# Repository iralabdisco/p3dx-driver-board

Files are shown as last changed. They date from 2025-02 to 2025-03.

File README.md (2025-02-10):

# p3dx-driver-board
An effort to reverse-engineer the Adept MobileRobots Pioneer-3DX's driver board.

## Rationale

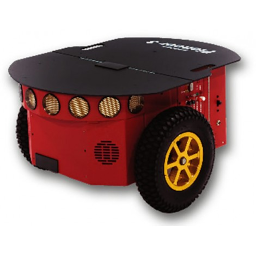
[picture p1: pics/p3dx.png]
p3dx


The [P3DX](https://www.generationrobots.com/media/Pioneer3DX-P3DX-RevA.pdf) is a nice, featureful, and self-contained robotics platform that was released sometime in the early '00s. We have three of those in our laboratory, and they're currently big red paperweights, as their SDK is no longer mantained; to my knowledge, the ROSARIA module that was used with ROS1 to control those robots has not been ported to ROS2, and their ARIA protocol is not documented.

There've been some efforts to produce libraries that can interface with the on-board microcontroller by figuring out how the protocol works, like [Purdue's P2OS driver](https://github.com/allenh1/p2os/tree/main), which is an open-source module for ROS that includes an ARIA driver -- their (C++) packet driver is under `p2os_driver/packet` and `p2os_driver/sip`.

I like the construction and the modularity of the P3DX: the driver board is completely separated from the MCU board, probably because the original designers already had upgradability in mind, and they're connected through a ribbon cable. Since the MCU board is not integral to the operation of the robot's electronics, I decided to figure out the pinout of the ribbon cable so that we could try to attach a different MCU or a Raspberry Pi to the driver board without too much effort, so that our students may still play with the P3DXes and learn from their operation.

## Architecture

The driver board has:
- Power control and generation circuitry for the +12V and +5V rails;
- Two H-bridges -- one for each motor;
- Connections for IR sensors and encoders;
- Optional connections for a fan, a charger, and temperature sensors to be mounted on the motors;

There are a couple of ICs on the board: two STM TD340 MOSFET drivers to control the H-Bridge, a couple of STM TS922I Op-Amps, and two TI SN74HC14 Schmitt-Trigger Inverters. Look under the [datasheets/](datasheets/) folder if you need to look something up.

## Disclaimers

Obligatory disclaimers:
- I take absolutely no credit for the design of the driver board.
- This was an independent effort I made in my spare time; my institution is not affliated with this in any way, shape, or form.
- I decided to release the schematics I came up with under Public Domain because, as far as I know, this platform has been long since abandoned. If you feel like this is infringing your IP rights, please file a DMCA request and I'll take this down.

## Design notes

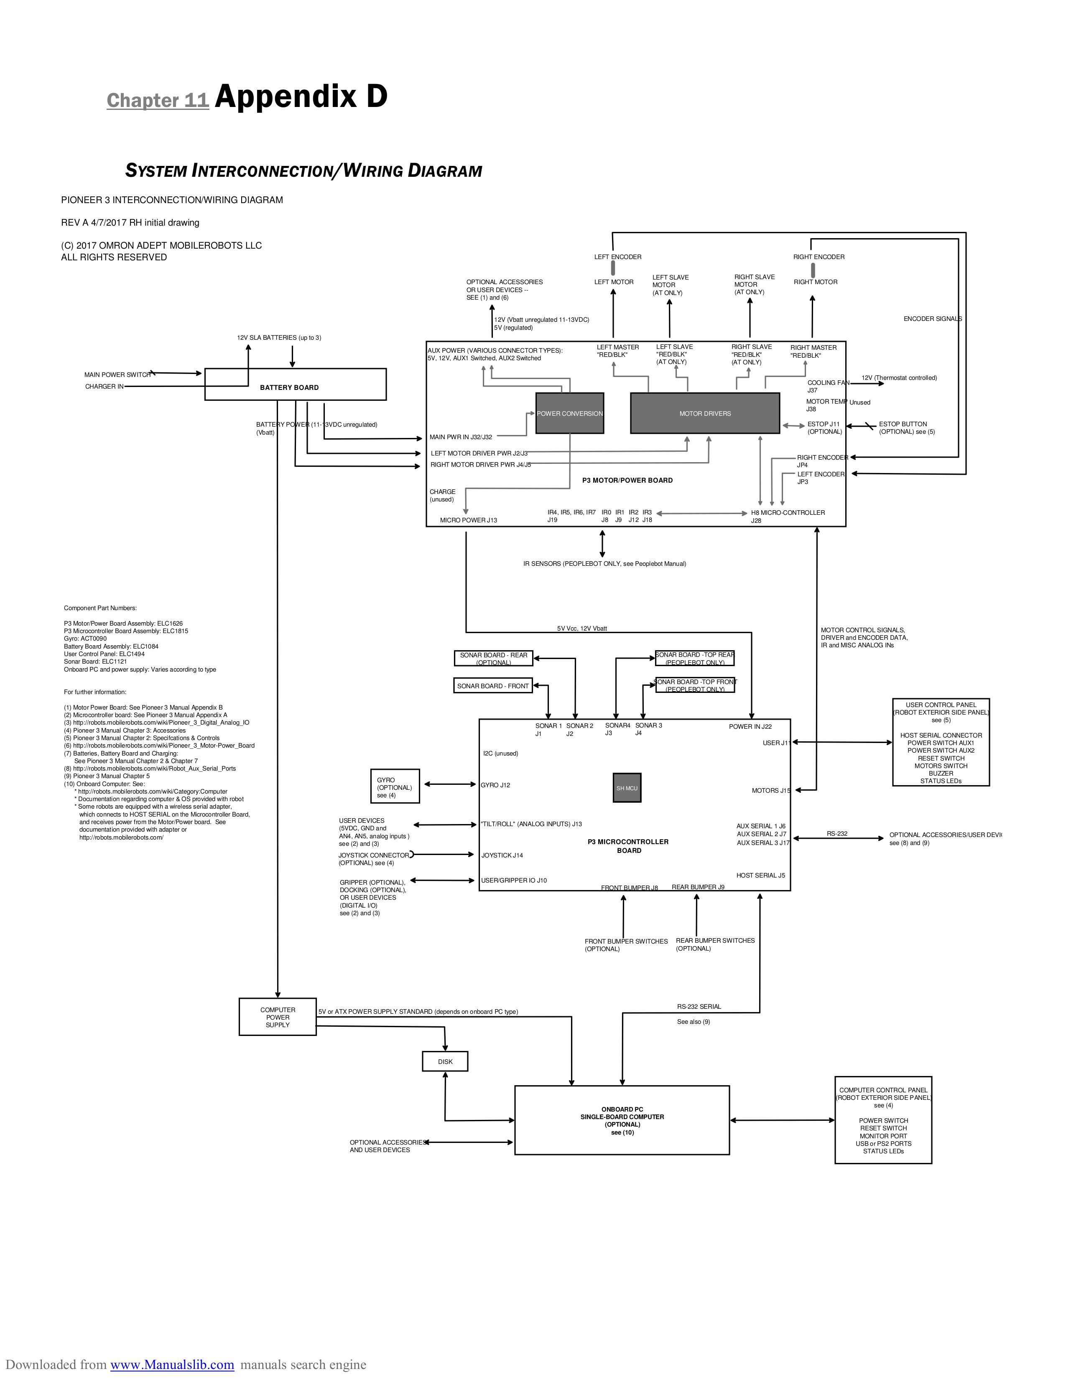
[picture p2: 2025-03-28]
datasheets/system_interconnection.jpg

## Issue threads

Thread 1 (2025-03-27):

Funzionamento Ponte-H (TD340)

giuseppe-caliaro, 2025-03-27:
Il circuito integrato ST TD340 permette il pilotaggio di un motore DC attraverso un ponte-H.
Di seguito il diagramma a blocchi e la descrizione del pinout.

_**Diagramma a blocchi/Descrizione pinout TD390**_

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

Punti chiave appresi:
L1/L2 = Pilotano i gate dei mosfet low-side del ponte-H, Q1L e Q2L rispettivamente in figura.
H1/H2 = Pilotano i gate dei mosfet high-side del ponte-H, Q1H e Q2H rispettivamente in figura.
S1/S2 = Costituiscono insieme a CB1 e CB2 il circuito di bootstrap, necessario quando il

Closed 2025-03-28.

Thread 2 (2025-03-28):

Funzionamento TD340 (Motor Driver)

giuseppe-caliaro, 2025-03-28:
Il circuito integrato ST TD340 permette il pilotaggio di un motore DC attraverso un ponte-H.
Di seguito il diagramma a blocchi e la descrizione del pinout.

**_Diagramma a blocchi/Descrizione pinout TD340_**
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

**Punti chiave appresi:**

- L1/L2: Pilotano i gate dei mosfet low-side del ponte-H, Q1L e Q2L rispettivamente in figura.

- H1/H2: Pilotano i gate dei mosfet high-side del ponte-H, Q1H e Q2H rispettivamente in figura.

- S1/S2: Costituiscono insieme a CB1 e CB2 il circuito di bootstrap del ponte H.
Il circuito di boostrap è necessario per superare la tensione di soglia (Vgate - Vsource) del mosfet high-side quando quest'ultimo è ON.
Perchè è necessario? È necessario perchè in questa configurazione Source del mosfet high-side è a 12V, quindi non si raggiungerebbe la tensione di soglia minima per garantire l'attivazione mosfet.
Diversamente nei mosfet low-side ciò non accade, essendo source a GND quando i mosfet low-side sono attivi.
vedi https://www.homemade-circuits.com/h-bridge-bootstrapping

- IN1/IN2: Questi pin sono utilizzati per controllare velocità (IN1) e direzione (IN2) del motore. La modalità "freno" è attivata quando ci sono 0V sul pin IN1 per piu di 200 microsecondi.

**Questioni aperte:**

1. Nel circuito sono presenti due Op-Amp U6A/U6B (fisicamente uno solo, Op-Amp TS9221 presenta due ingressi invertenti, due ingressi non invertenti e due output). Non mi è completamente chiaro il loro utilizzo.
U6A sembra essere configurato come comparatore (vedi partitore di tensione su ingresso invertente)
U6B avendo una retroazione positiva (vedi Vout applicata a ingresso non invertente) sembra essere un comparatore con isteresi (Trigger di Schmitt).
L'uscita dell'Op-Amp U6B controlla la base di un BJT, il quale agisce come interruttore per i segnali RIGHT_C1 e RIGHT_C2 provenienti dalla MCU.

Non mi è chiaro il motivo del collegamento del Drain di Q5 con il circuito sopra citato.
Non trovo riscontro di continuità con questo collegamento _DrainQ5 - R36 - Ingresso non invertente U6A_ ,  mentre trovo riscontro di continuità con _SourceQ7 - R36 - GND_ , il mosfet Q7 costituisce parte del low-side del ponte H quindi è sensato che il Source sia a GND.

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

Per un controllo di base del TD340, IN1 e IN2 sono sufficienti, tuttavia, la comprensione del circuito sopra descritto penso sia fondamentale per decifrare la logica di controllo dei segnali MCU verso il TD340.

jack23247, 2025-03-28:
Ottimo lavoro.

Ti lascio qui una risorsa interessante sui ponti H: https://www.modularcircuits.com/blog/articles/h-bridge-secrets/

Per quanto riguarda Q5, ci guardiamo insieme quando posso. Gli opamp anche, ma non sono molto ferrato.. quattro occhi sono sempre meglio di due però

giuseppe-caliaro, 2025-03-28:
Credo di aver capito che:
Gli ingressi degli operazionali sono collegati a Source di Q7 e Q8 (low-side), attraverso questi mosfet scorre la corrente che scorre attraverso il motore.
Interposta tra questo collegamento è posizionata una resistenza di shunt (R2 nello schema), la quale viene normalmente utilizzata come misuratore di corrente (qui una discussione circa la misurazione di corrente attraverso l'utilizzo di una resistenza di shunt https://electronics.stackexchange.com/questions/152500/measure-current-through-h-bridge-using-shunt).

La caduta di tensione ai capi della resistenza di shunt è proporzionale alla corrente che scorre attraverso i mosfet.
Se si dovesse verificare un overcurrent, causerebbe una caduta di tensione, probabilmente sotto una certa soglia dimensionata nell'implementazione degli op-amp. Questa caduta di tensione pilota il BJT, bloccandone la conduzione e interrompendo cosi i segnali RIGHT_C1 e RIGHT_C2.

Sostanzialmente mi sembra di aver capito che è un circuito di protezione da overcurrent.

giuseppe-caliaro, 2025-03-28:
Condivido il nuovo schema (Right motor driver) aggiornato con le correzioni riguardanti gli op-amp discussi precedentemente:

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

giuseppe-caliaro, 2025-03-29:
**Ulteriori note interessanti circa il funzionamento del driver TD340:**

- Frequenza di switching: 25kHz

- Lavora con una tensione tra 6.5V e 18.5V

- Da datasheet: _"The speed control (or duty cycle) is achieved by the Low Side Drivers which impose the PWM function while the cross-corresponding High Side MOSFETS is kept fully ON."_.
Questa tecnica consiste nell'applicare il segnale PWM ai mosfet low-side, cioè quelli connessi a massa, mentre i mosfet high-side, cioè quelli connessi alla tensione di alimentazione, vengono mantenuti sempre ON.

- Ci sono 4 pin che forniscono servizi aggiuntivi:

1. **Reset**: TD340 fornisce un circuito di supervisore di tensione, il quale riavvia il microcontrollore quando la tensione di quest'ultimo scende sotto una soglia di 4.2V, e l'uscita Reset resta a LOW fino a quando la tensione non supera i 4.3V, dopodichè il microcontrollore riprende la sua normale esecuzione.

1. **Watchdog** (WD nello schema): TD340 fornisce un circuito di watchdog, il quale resetta il driver per evitare che il sistema rimanga bloccato in caso di errori software/hardware. Watchdog controlla che il microcontrollore invii segnali costanti al pin WD, se questi impulsi non avvengono per un periodo troppo lungo (timeout, settabile attraverso il dimensionamento di un condensatore), questo blocca il sistema finchè il microcontrollore non riprende ad inviare impulsi al pin WD.

1. **Temp**: TD340 fornisce un indicatore di temperatura.

1. **Standby** (STBY nello schema): TD340 può essere messo in standby mode tramite software, i mosfet vengono spenti. Questo permette di ridurre il consumo a 200 microAmpere. Per uscire da questa modalità il sistema ha bisogno di 20 ms per caricare il condensatore facente parte del circuito di boostrap. Il driver non deve ricevere segnali IN1 e IN2 prima che il condensatore sia completamente carico, altrimenti i mosfet high-side potrebbero non funzionare correttamente.

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

Da schema i sopracitati pin ad eccezione di Standby risultano però essere stati esclusi nel design della driver-board.
La configurazione di Standby come accennato non risulta essere esclusa, tuttavia dal connettore del microcontrollore non sembra essere presente un pin designato a questa funzione:

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

Questa questione è cruciale per la sicurezza e l'affidabilità complessiva del sistema, poiché, con l'esclusione dei pin relativi a Reset e Watchdog nel design della driver-board, la gestione delle sicurezza e affidabilità è completamente delegata al microcontrollore STM32F767ZI (MCU scelta per pilotare la driver-board).
Credo quindi che sarà necessario tenere conto di questo aspetto in fase di sviluppo.

jack23247, 2025-03-31:
Ottimo lavoro. Alcune osservazioni:

- Bello e leggibile lo schema. Al posto del motore però metterei il connettore, dato che il motore non è tecnicamente parte della scheda. Possiamo comunque mettere il motore in un box per chiarezza.
- Avevo notato anche io il fatto che non è stato usato il circuito di Watchdog interno ai TD340. Non so il perché di questa scelta, ma sicuramente ci sarà stato un motivo ingegneristicamente valido. Comunque teniamone conto.

Per quanto riguarda i "salti", quando passo in lab ci guardiamo insieme!

giuseppe-caliaro, 2025-03-31:
Perfetto, allora modifico lo schema sostituitendo il motore con il connettore.

Per la questione watchdog magari studiando l'interfacciamento tra la nostra board e la driver-board salta fuori il motivo dell'esclusione di questi pin.

giuseppe-caliaro, 2025-03-31:
Il modello è: **Renesas SH2-7144 RISC 32-bit**.
Documentazione: https://www.renesas.com/en/document/mah/sh7144-group-sh7145-group-hardware-manual?r=1054851

Che succede se imposti il duty cycle del PWM a zero? E come passi, in generale, il segnale PWM al driver?

Impostando il duty cycle del PWM a zero mi aspetto che il Driver setti a 0V il motore.

In generale, penso che il microprocessore della Nucleo generi il segnale PWM (attraverso un timer).
La Nucleo sarà collegata, attraverso il connettore specifico, alla driver-board, la quale invia il segnale PWM al pin del Driver.

jack23247, 2025-03-31:
Ottimo! Allora possiamo gestirlo così anche noi, secondo me.

giuseppe-caliaro, 2025-04-01:
> * STBY è attivo basso (ha la linea sopra), quindi se non erro R41 fa da resistenza di pull-up e fondamentalmente esclude la funzionalità di Stand-by.

Grazie per la precisazione

Closed 2025-05-22.

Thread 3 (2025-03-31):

Motor Encoder

giuseppe-caliaro, 2025-03-31:
Prima di analizzare il connettore J28, cioè il connettore che collega MCU-board e driver-board e permette di scambiare segnali tra di essi, è secondo me necessario approfondire prima i segnali che il sopracitato connettore trasporta e come quest'ultimi sono generati.
Nella issue relativa all'integrato TD340 ho analizzato i segnali che arrivano da J28 al driver che infine pilota i motori, cioè IN1 e IN2.

In questa issue analizzerò i connettori JP3 e JP4, che al contrario dell'integrato TD340, inviano segnali dai motori al microprocessore, cioè i segnali di encoding.

Di seguito lo schema dei pin del connettore J28:

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
Questa issue descrive i pin: 6, 8, 10, 12, cioè rispettivamente:

- Left encoder channel A

- Right encoder channel A

- Right encoder channel B

- Left encoder channel B

La driver-board del Pioneer P3DX offre un encoder ottico a quadratura, detto anche incrementale, il quale genera sulle sue uscite due segnali A e B, cioè due onde quadre con un duty cycle del 50% sfasate di 90°

Per conoscere se il motore gira in senso orario o antiorario, si confrontano le due fasi di A e B.
Sul fronte di discesa della fase A, se il valore logico di B è 1, il motore sta ruotando in senso orario, viceversa, cioè se il fronte di discesa di A corrisponde al valore logico di B 0, il motore sta ruotando in senso antiorario:

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
**_Senso orario/Senso antiorario_**

---

Da manuale operativo (Pag. 67) , ho trovato i seguenti dati che secondo me saranno utili in fase di sviluppo firmware per ottenere valori di velocità/rotazione/distanza percorsa ecc. :

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
- **Encoders**: 500-count quadrature optical encoder on each motor: l'encoder quindi genera 500 impulsi (A e B) per ogni giro completo del motore
- **Quadrature encoder count/wheel revolution**: 19,150 (200mm wheel): l'encoder genera 19.150 impulsi per ogni giro completo di ruota assumendo che quest'ultima abbia un diametro di 200mm.
- **Quadrature encoder counts/mm robot linear distance travelled**: 128: l'encoder genera 128 impulsi per millimetro di distanza percorsa.
- **Quadrature encoder counts/360° robot rotation**: 33,140: l'encoder genera 33.140 impulsi per una completa rotazione di 360° sul suo asse.

---

Di seguito riporto lo schema degli encoder presenti sulla driver-board:

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

I segnali, rispettivamente dal pin 1 e 8 dell'encoder, passano attraverso un'integrato, il 74HC14, cioè un Trigger di Schmitt.
Il Trigger di Schmitt produce in uscita un'onda quadra "pulita" da rumore ed eventuali oscillazioni e squadra perfettamente il segnale fornito dagli encoder.

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

Successivamente il segnale è fornito al microprocessore attraverso i segnali EL1, EL2, ER1, ER2, pronti per essere processati.

giuseppe-caliaro, 2025-03-31:
Mastering STM32 2.0.1 Pag. 325 paragrafo 11.3.9 **Encoder Mode**  spiega come gestire segnali di encoder in quadratura.
Segnali di encoder in quadratura possono essere gestiti con degli interrupt "_using interrupts
to capture when the channel changes status_", oppure usando dei timer.

STM32 fornisce fornisce anche una modalità dei timer detta  _encoder mode_.
Questa modalità offre, settando in modo corretto i parametri di un timer, la direzione del motore direttamente in un registro (TIMx_DIR),

Sarebbe interessante in seguito approfondire e discutere quale modalità utilizzeremo per gestire i dati forniti dall'encoder.

Closed 2025-05-22.

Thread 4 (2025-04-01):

Motor Enable & E-STOP Button

giuseppe-caliaro, 2025-04-01:
Procedo con l'analisi dei segnali trasportati dal connettore J28 (MCU connector) relativa ai pin 5 e 7, rispettivamente ME (Motor Enable) e E-STOP:

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

La driver-board del Pioneer P3DX è equipaggiata da due segnali di sicurezza:

-**ME**: Motor Enable è un segnale che deve essere settato ad HIGH dal microcontrollore affinchè i motori del Pioneer possano funzionare. Questo segnale è utile in caso di scollegamento accidentale della MCU, difatti questo evento provocherebbe il passaggio dello stato da HIGH a LOW (vedi l'utilizzo della resistenza R52 affinchè il pin 5 non rimando "floattante".

-**E-STOP**:
Pag. 6 Manuale operativo
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
Pioneer P3DX ha opzionalmente un pulsante di emergenza "_STOP_" il quale ha la funzione di stoppare immediatamente i motori.

Come suggerisce lo schema (pin E-STOP è a GND), la driver-board (indica di rimuovere R59 per abilitare l'E-STOP, con R59 presente) e la scocca del Pioneer stesso (non presenta alcun pulsante di STOP) credo che si possa trarre la conclusione che il pulsante non sia presente in questo modello di Pioneer.

**_Pulsantiera di controllo Pioneer_**
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

---
**_Indicazione di rimuovere R59 per abilitare l'E-STOP_**
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

**Questioni aperte:**

1. Discutendo ad inizio progetto delle funzionalità del Pioneer ricordo che la funzione di E-STOP fu nominata, potremmo metterla nel backlog delle cose da fare, cosa ne pensi?

giuseppe-caliaro, 2025-04-02:
Condivido lo schema aggiunto riguardante l'E-STOP INPUT:

_**Con R59**_
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

_**Senza R59**_
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

_**Driver-board**_
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

Di seguito quello che ho capito:
Nel connettore J11 dovrà essere collegato un pulsante normalmente aperto, che in condizioni di riposo lascerà il circuito aperto. Rimuovendo la resistenza R59, come indicato dalla serigrafia sulla scheda, il segnale dell’E-STOP sarà libero di commutare. In questo modo, quando il pulsante non viene premuto, il segnale rimarrà alto grazie alla resistenza R45, mentre alla pressione del pulsante verrà forzato a GND, attivando così la funzione di arresto di emergenza. Questa modifica permetterà di gestire correttamente il segnale E-STOP sul pin 7 del microcontrollore.

Considerando anche gli schemi condivisi, la logica di funzionamento descritta ti risulta corretta?

jack23247, 2025-04-07:
A me suona bene. Gestire un input attivo basso, nel caso in cui volessimo utilizzare questo pin, non dovrebbe essere un problema per l'STM32

giuseppe-caliaro, 2025-04-07:
Perfetto.
Potremmo, come discusso in laboratorio, collegarci il classico emergency stop button rosso per spegnere completamente il robot in caso di "emergenza"

jack23247, 2025-04-08:
Si, anche se io considererei la possibilità di attaccare il pulsante di emergenza in serie con i motori per evitare proprio che passi per l'elettronica

giuseppe-caliaro, 2025-05-16:
Come discusso in laboratorio, il mistero di Motor Enable è stato svelato, è un pin del connettore J28 che non è stato implementato, ma Pull-Downato.
Avendo già discusso ampiamente dell'E-Stop button, chiuso la issue come completata.

Closed 2025-05-16.

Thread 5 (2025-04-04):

User Control Panel

giuseppe-caliaro, 2025-04-04:
User Control Panel è un pannello di controllo posizionato a lato del Pioneer.
Vi sono presenti:

- 4 Pulsanti:
1. **AUX1**
2. **AUX2**
1. **RESET**
1. **MOTORS**

- 7 Led:
1. Due led relativi alla trasmissione e ricezione della porta seriale
2. Due led relativi ai pulsanti AUX1 e AUX2
3. Un led relativo allo stato della batteria
4. Un led di stato (STAT)
5. Un led di PWR, probabilmente un led di stato dei motori (ON/OFF)

Inoltre sono presenti un buzzer e una porta seriale.

---

**Pannello Pioneer P3DX:**
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

**PCB pannello**
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

**Pinout connettore MCU-Pannello (Lato MCU)**
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

Al fine di utilizzare nel modo corretto gli elementi presenti sul pannello, è necessario capirne il funzionamento.

Sulla scheda è presenta un circuito integrato, il 74HC00, il quale è  costituito da 4 NAND, le quali condividono lo stesso ingresso (quindi parliamo sostanzialmente di NOT).

Di seguito il pinout del 74HC00 da datasheet:

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

Non mi però è del tutto chiaro il funzionamento dell'integrato, soprattutto per quanto riguarda la gestione degli ingressi e delle uscite:

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

giuseppe-caliaro, 2025-04-04:
Condivido lo schema relativo alla **porta seriale** presente sulla scheda del pannello:

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

giuseppe-caliaro, 2025-04-04:
Condivido lo schema relativo al **buzzer** presente sulla scheda del pannello:

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

giuseppe-caliaro, 2025-04-04:
Condivido lo schema relativo ai **pulsanti** e relativi **led** presenti sulla scheda del pannello:

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

giuseppe-caliaro, 2025-04-04:
Rimane dunque da chiarire la questione relativa all'integrato 74HC00 e i relativi pin IN/OUT, i quali probabilmente gestiscono il led relativo alla stato della batteria

giuseppe-caliaro, 2025-04-05:
Ulteriori note interessanti riguardo il funzionamento dello User Control Panel (ARCOS based, quindi MCU e Firmware proprietario):
Da Manuale Operativo:

-**Led batteria:**
_Pag. 14:_
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
_Pag. 11:_
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

---

-**Led PWR, Led STAT:**
_Pag. 10:_
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

---

-**Buzzer:**
_Pag. 11:_
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

---

-**Serial Port:**
_Pag. 11:_
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

---

-**Power Switches (AUX1/AUX2 buttons):**
_Pag. 11:_
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

---

-**Reset/Motors buttons**
_Pag. 11/12:
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

---

Concludo dicendo che secondo me sarebbe utile chiarire cosa vogliamo effettivamente replicare del pannello originale, soprattutto per quanto riguarda i due pulsanti degli AUX power switches: potremmo considerarli, come suggerito da te in laboratorio,  semplicemente come pulsanti utente, da usare liberamente per altre funzioni, non per forza legati all’alimentazione.

giuseppe-caliaro, 2025-04-05:
Questo è quello che sono riuscito a capire riguardante al circuito del led relativo alla batteria e il circuito integrato 74HC00:

Il diodo led è bicolor, perchè a differenza dei led RGB a tre pin, il led in questione ne presenta due.
Quando la corrente scorre attraverso il diodo in un verso, emette luce verde, quando la corrente scorre nel verso opposto, emette luce rossa. (vedi: https://www.quarktwin.com/blogs/led/bi-color-led-working-principle/21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)

L'integrato 74HC00 viene utilizzato per creare una differenza di potenziale e permette alla corrente di scorrere in un verso o nel verso opposto.

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

Quando PLED (che arriva dal microcontrollore, il quale è processato secondo la tensione della batteria) ha valore HIGH, l'uscita di U1B è 0V, mentre l'uscita di U1A è 5V, questo permette alla corrente di scorrere in un verso.
Viceversa quando PLED ha valore LOW, l'uscita di U1B è 5V, mentre l'uscita U1A è 0V, questo permette alla corrente di scorrere nel verso opposto.

Da Manuale Operativo:
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
L'arancione credo che venga ottenuto con un segnale PWM generato dal microntrollore, il quale commutando ad alta frequenza il verso della corrente, genera il colore arancione/giallo.

jack23247, 2025-04-07:
Ottimo lavoro. L'unica cosa che cambierei è il simbolo usato per i pulsanti e quello usato per i toggle switch (oppure aggiungerei una nota).

Io sinceramente lascerei AUX1 e AUX2 programmabili dall'utente. L'interfaccia seriale a 3 pin potremmo sia usarla che scartarla e collegare direttamente l'UART alla scheda. Idealmente direi di mettere dei jumper per permettere agli utenti di fare quello che vogliono.

Molto interessante il LED bicolore per il controllo del voltaggio batteria... anche se mi sembra un po' over-engineered. Possiamo pilotarlo dal micro oppure prendere un integrato che faccia da comparatore/voltmetro. Oppure collegare direttamente un voltmetro a 7 segmenti e non usare quel LED, che forse è anche meglio.

giuseppe-caliaro, 2025-04-07:
Grazie per i suggerimenti, provvedo quindi a modificare lo schema.

Riguardo ad AUX1 e AUX2, potremmo discutere di quale funzionalità assegnare loro in base alle nostre esigenze.

L'idea del voltmetro con display a 7 segmenti mi sembra ottima, possiamo in tal modo monitorare il valore esatto di tensione delle batterie.

Closed 2025-05-22.

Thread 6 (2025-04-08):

Sonar

giuseppe-caliaro, 2025-04-08:
In questa issue riporto quello che ho capito analizzando il funzionamento dei sonar e le modalità di interfacciamento con quest'ultimi.

Pioneer P3DX ha in dotazione un'array di 8 sensori ultrasuoni utilizzati per la rilevazione ostacoli:
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

I sensori sono posizionati secondo il seguente schema:
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

Al fine di comunicare con la MCU, viene utilizzata la seguente PCB di interfacciamento:
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
La scheda presenta i seguenti elementi degni di nota:

Due connettori, il primo a 16 pin (centrale), è utilizzato per comunicare con gli 8 sensori, il secondo (di destra) a 10 pin è utilizzato per comunicare con la MCU e presenta il seguente pinout:
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
Dove:
- A0, A1, A2 sono dei segnali usati da un demultiplexer (3 ingressi, con 2^3 = 8 uscite), mi permettono quindi di selezionare gli 8 sensori.
- BINH: Segnale che permette di disabilitare la rilevazione tramite i sensori.
- INIT: Segnale che invia il ping del sensore selezionato.
- ECHO: Segnale che riceve l'eco del sensore selezionato.
- Vcc
- GND

Altri elementi presenti sulla scheda che permetto l'effettivo funzionamento dei sensori sono:
- TL851 SONAR RANGING CONTROL
- TL852 SONAR RANGING RECEIVER
- 74HC138N 3-to-8 DEMULTIPLEXER
- AQW214 PhotoMOS RELAYS

Mi limito a citarli non essendo i sensori il focus di questo progetto.

---

Al fine di controllarli ed ottenere i valori desiderati, mi aspetto quindi che la Nucleo debba controllare iterativamente gli 8 sensori, modificando a tal fine A0, A1 e A2, per ogni sensore inviare un segnale di INIT, aspettare l'ECHO, calcolare il tempo trascorso (ECHO - INIT)  ed infine conoscendo a priori la velocita di propagazione del suono nell'aria, possiamo ricavare la distanza (d = v * t).

jack23247, 2025-04-15:
Ottimo lavoro, direi che spostiamo in Halted per il momento dato che a noi i SONAR ora non servono.

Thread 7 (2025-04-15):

Integrazione Nucleo↔Driver-Board

giuseppe-caliaro, 2025-04-15:
In questa issue discuterò l'integrazione della Nucleo stm32 F767ZI con la driver-board del Pioneer 3DX, inizalmente dal punto di vista elettrico/alimentazione, e succcesivamente dal punto di vista della gestione dei segnali (PWM per controllo motori, lettura encoder, pulsanti ecc.)

- **Alimentazione**
Da User manual STM32 Nucleo-144 boards Pag. 22:

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

Come descritto la Nucleo può essere alimentata in tre modi differenti, Vin, E5V e 3.3V, tutti con un loro range di tensioni tollerate e un limite di assorbimento di corrente.

Essendo la driver-board del Pioneer alimentata a 5V per la gestione della circuiteria di controllo dei motori e per l'interfacciamento con la MCU proprietaria, e 12V per alimentare i due motori DC, credo che sia corretto supporre che utilizzeremo la modalità E5V per alimentare la Nucleo.
Questo implica come specificato dal manuale nel settare corretamente il jumper di JP3 per selezionare l'alimentazione corretta, e rimuovere il jumer di JP1 per eliminare il limite a 100mA di assorbimento di corrente.

Come mostrato nella figura sottostante la driver-board fornisce i 5V per alimentare la MCU attraverso il connettore J13, mentre lato MCU proprietaria il connettore è collegato a J22
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

Il pinout del connettore J13 è il seguente:

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
Di questi pin solo i pin 1,2,3 raggiungono l'MCU proprietaria.
Oltre ai 5V, il connettore J13 fornisce 12V , i quali sono utilizzati dallo User Control Panel, attraverso il connettore J11 (come si vede sopra in figura), per l'array di Sonar e vari componenti ausiliari come Joystick e giroscopio.

Fammi sapere se l'analisi relativa all'alimentazione della Nucleo è secondo te corretta.

giuseppe-caliaro, 2025-04-15:
Condivido inoltre una sequenza definita **_mandatory_**:

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

Spiega quali siano i passaggi per alimentare esternamente la Nucleo e avere comunque la possibilità di flashare o debuggare attraverso l'USB di debug, evitando di riscontrare i problemi descritti nell'immagine sopra.

giuseppe-caliaro, 2025-04-15:
Intendi la questione jumper JP3? In tal caso sì ho fatto qualche esperimento alimentando la Nucleo esternamente ed è molto semplice

giuseppe-caliaro, 2025-04-16:
**- PWM e direzione motori**
Al fine di controllare i motori del Pioneer, come abbiamo discusso nella issue dedicata all'IC TD340, la Nucleo deve generare 4 segnali:
1. PWM motore sinistro
2. PWM motore destro
3. Segnale HIGH/LOW per direzione motore sinistro
4. Segnale HIGH/LOW per direzione motore destro

La famiglia STM32F7, alla quale appartiene la nostra Nucleo, fornisce diversi timer per la gestione del segnale PWM, in particolare fornisce quattro timer General purpose: TIM3 e TIM4 a 16 bit, e TIM2 e TIM5 a 32 bit, come mostrato in figura;
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

Da datasheet dell'IC TD340, la frequenza massima con la quale è in grado di commutare il segnale è di 25KhZ.
Credo quindi che possiamo optare per l'utilizzo dei timer TIM3 e TIM4 a 16 bit e ottenere comunque una risoluzione più che sufficiente in termini di sottolivelli. (Esempio potrei impostare ad 1 il prescaler, quindi utilizzare senza divisori direttamente la  frequenza massima del clock del sistema ottenendo addirittura 3839 sottolivelli, quindi penso che 16 bit siano più che sufficienti per un controllo preciso dei motori).

Posso quindi impostare il pin GPIO **PA6** come TIM3_CH1 (PWM Generation Channel 1 attraverso il timer TIM3) e **PD12** come TIM4_CH1 (PWM Generation Channel 1 attraverso il timer TIM4).
Questi due segnali permettono quindi di controllare la **velocità del motore** di destra e del motore di sinistra del Pioneer.

---

Per quanto riguarda la gestione della **direzione dei motori**, l'IC TD340 richiede come detto prima un segnale per motore.
Il valore di questo segnale deve essere HIGH o LOW e determina il senso di rotazione del motore.
A questo scopo penso che possiamo utilizzare due pin GPIO qualsiasi, magari tenendo conto semplicemente di non utilizzare dei pin GPIO che possono implementare Alternate Function particolari, così da evitare di utilizzare inutilmente un pin GPIO con funzionalità avanzate per un semplice toggle.

---

Fammi sapere se questa analisi ti sembra corretta così procedo oltre.

giuseppe-caliaro, 2025-04-17:
Intanto confermo che da datasheet PE9 e PE11, e PA0 e PA1 sono 5V tolerant, nella colonna _I/O Structure_ **FT** significa 5V tolerant:

**_PE9/PE11_**
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

**_PA1_**
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

**_PA0_**
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

jack23247, 2025-04-18:
- Ottima analisi. Per i pin puoi guardare il firmware scritto da Federica per Otto che trovi sul GitHub di IRALab per vedere che pin ha usato lei all'epoca
- Per passare a 3v3 a segnali TTL possiamo usare un level-shifter che ci fa anche da buffer

jack23247, 2025-04-18:
Per gli input non lo so. Usare un level-shifter è problematico perché potrebbe distorcere il segnale che arriva dagli encoder in maniera troppo significativa.

giuseppe-caliaro, 2025-04-22:
Per quanto riguarda l'incompatibilità dei segnali output di **direzione** e **PWM** con la driver-board del Pioneer potremmo utilizzare un **Logic Level Shifter** come quello mostrato in figura:

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

giuseppe-caliaro, 2025-04-22:
Analizzando il percorso che i segnali seguono dal connettore _Motors_ presente sulla MCU proprietaria noto che:
- I segnali di **PWM** e **Direzione** provenienti dal processore prima di arrivare al connettore ed essere trasmessi alla driver-board passano attraverso ad un **HCT541**.
HCT541 è un buffer non invertente, il quale ha il compito di ripetere i segnali in uscita, amplificandone la corrente e isolando unidirezionalmente la MCU (quindi anche proteggendola) dalla driver board.
- I segnali di **Encoding** (lo stesso vale per i segnali provenienti dai sensori di prossimità) provengono invece dal connettore e prima di arrivare al processore passano attraverso un **LVC541A**.
L' LCC541A, come l'HCT541 è un buffer, con la differenza che opera con tensioni di uscita minori. Questo perchè i progettisti della MCU-board del Pioneer hanno dovuto interfacciarsi con due tensioni differenti (come noi), quella dei segnali di encoding a 5V e quella dei pin del processore a 3.3V (difatti sono presenti due regolatori di tensione **LT1086** sulla MCU-board, uno per alimentare il processore, l'altro per alimentare i due integrati **LVC541A**, uno per i segnali di encoding l'altro per i sensori di prossimità).

Penso quindi che i due integrati sopra descritti, l'**HCT541** e il **LVC541A** possano essere una soluzione concreta anche per il nostro problema di interfacciamento.

Cosa ne pensi? I due integrati, alimentati rispettivamente a 5V l'integrato che gestisce direzione e PWM e 3v3 l'integrato che gestisce i segnali di encoding, sono quindi dei Level Shifter che possiamo utilizzare?

giuseppe-caliaro, 2025-04-23:
Assumendo che il ragionamento relativo agli integrati che ho descritto precedentemente sia corretto, ho fatto una prima bozza di come collegherei la Nucleo e la driver-board attraverso la board di interfaccia:

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
Qualche considerazione:
- Devo assicurarmi di cortocircuitare a GND i segnali di Enable degli integrati HCT541 e LVC541A al fine di attivarne le uscite.
- LVC541A assorbe corrente nell'ordine delle decine di mA, quindi penso che la Nucleo riesca a gestirle. Possiamo comunque con un regolatore di tensione abbassare i 5V provenienti dalla driver-board a 3v3 e alimentare direttamente l'integrato, evitando così di sovraccaricare inutilmente la Nucleo. Lo schema in questione è infatti quello consigliato da datasheet:
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

- Da datasheet viene raccomandato di mettere a GND tutti i pin non utilizzati:
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
- Utilizzare un bypass capacitor per il pin di Vcc per evitare dei disturbi dell'alimentazione: _Each VCC pin should have a good bypass capacitor to prevent power disturbance. For devices with a single supply, 0.1 μf is recommended;_

giuseppe-caliaro, 2025-04-30:
Per quanto riguarda la questione latenza introdotta dai buffer, da datasheet l'IC HCT541 introduce un ritardo _tipico_ di 12 ns, mentre l'IC LVC541A introduce un ritardo _massimo_ di 5.1 ns.

jack23247, 2025-05-02:
Ok, come vedi l'integrato migliore è stato usato per gli encoder perché sono più sensibili alla latenza. Controlla anche la tensione max che possono fornire i due IC

giuseppe-caliaro, 2025-05-09:
Come discusso in laboratorio, è sensato "mappare" tutti i segnali che provengono da J11 e J28 al fine di poterli utilizzare per implementazioni future, ad esempio per la gestione dei sensori oppure per la gestione dei pin analogici, senza modificare radicalmente l'Interface-Board o crearne una nuova.

A tale scopo serve ridefinire lo schema condiviso in precedenza, sia per gestire i segnale della porta seriale (come discusso nella issue di integrazione dello User Control Panel) sia per gestire tutti quei segnali che da J11 a J28 che al momento non sono gestiti dalla prima bozza di schema della Interface-Board.

- **Sensori IR**:
Dal connettore J28 abbiamo otto pin relativi ai sensori IR, uno per ogni sensore presente sul Pioneer. Dato che questi segnali devono essere adattati ad un livello di tensione corretto per la Nucleo, necessitano di un LVC541A, il quale ha esattamente otto ingressi.
Detto questo ciascuo degli otto bit relativi ai sensori devono essere gestiti tramite un pin GPIO in modalità Input.
Stm32 permette di leggere con una sola istruzione il registro di un'intera porta GPIO, dal registro IDR, quindi sarebbe sensato utilizzare un'intera porta GPIO per catturare questi dati, cosi da averne un accesso più rapido per gli sviluppi futuri.

- **Analog Input:**
Il connettore J28 trasporta due pin per degli ingressi analogici, i quali possono essere ad esempio i dati da un un giroscopio oppure un joystick. Questi segnali devono essere processati lato Nucleo da due convertitori analogico digitali.
La MCU Board proprietaria non gestisce direttamente i segnali dal connettore agli ADC, ma probabilmente passano attraverso una circuiteria necessaria ad adattare il livello di tensione. Al momento non ho ancora trovato riscontro di continuità di questi pin, quindi devo approfondire meglio la questione.
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
giuseppe-caliaro, 2025-05-10:
Studiando lato Driver-Board il segnale **Motor Enable** del connettore J28, noto che viene elaborato tramite un'ic, l'HC14 cioè un Trigger di Schmitt invertente (mostrato in figura).
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
Il segnale di Motor Enable arriva al connettore J28 attraverso le uscite di questo integrato, 1Y e 2Y. Testando l'integrato con il multimetro noto che gli ingressi 1A e 2A sono a massa. Questo mi fa pensare che in normali condizioni questo segnale è di Input alla MCU-Board, il quale avverte il processore di attivare o meno il segnale di PWM e direzione per attivare i motori.
Applicando un segnale alto agli ingressi 1A e 2A, le uscite dell'integrato sarebbero a LOW e di conseguenza anche il segnale di Motor  Enable, permettendo quindi al processore di avere un flag di quando ci siano o meno le condizioni di utilizzare i motori.

Purtroppo non riesco a capire sulla Driver-Board dove e come questo segnale viene commutato, potremmo guardare insieme in laboratorio.
In ogni caso, come detto prima, dobbiamo trattare questo segnale come segnale di Input della Nucleo, quindi dovrà essere adattato attraverso l'utilizzo dell'LVC541A.

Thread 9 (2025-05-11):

Interface-Board

giuseppe-caliaro, 2025-05-11:
Al fine di sostituire la MCU-Board proprietaria con la Nucleo, dobbiamo progettare una board che faccia da ponte tra la Nucleo, la Driver-Board e lo User Control Panel.

L'Interface-Board sarà alimentata attraverso il connettore **J13**, cioè un connettore posto sulla Driver-Board già progettato per alimentare la MCU-Board proprietaria. J13 è un connettore a tre pin il quale fornisce un'alimentazione di 5V, 12V e GND.
I 5V saranno utilizzati per alimentare l'Interface-Board e la Nucleo, mentre i 12V saranno utilizzati per alimentare lo User Control Panel.

Come discusso in laboratorio, l'interface-board dovrà avere due funzioni:
1)Adattare i segnali scambiati tra la Nucleo, la Driver-Board e lo User Control Panel.
2)Permettere un alloggio fisico per la Nucleo.

<h3>Adattamento dei segnali</h3>
Come discusso nella nelle issue di integrazione tra Interface-Board e Driver-Board  e Interface-Board e User Control Panel, i segnali devono essere adattati ad un livello logico gestibile dalla Nucleo e dalla Driver-Board.
Riassumo quanto appreso.

Vogliamo gestire tutti i segnali forniti dal connettore **J28**:
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

- Segnali di **PWM, Direzione**, cioè i pin 1, 2, 3, 4 provenienti dalla Nucleo verso la Driver-Board devono essere adattati da 3v3 a 5V, a questo scopo utilizzeremo un HCT541.

- Segnali degli **Encoder**, cioè i pin 6, 8, 10, 12 provenienti dalla Driver-Board verso la Nucleo devono essere adattati da 5V a 3v3, a questo scopo utilizzeremo un LVC541A.

-  Segnale di **Motor Enable**, cioè il pin 5, è ambiguo, risulta essere un segnale di Output sia lato MCU-Board sia lato Driver-Board. Lo tengo in standby fino a quando non siamo sicuri esattamente di come funzioni.

- Segnale di **E-Stop** cioè il pin 7,  proveniente dalla Driver-Board verso la Nucleo deve essere adattato da 5V a 3v3, a questo scopo utilizzeremo un LVC541A.

- Segnali di **Aux1 power enable** e **Aux2 power enable** sono attivati direttamente dalla pressione dei pulsanti Aux1 e Aux2 presenti sullo User Control Panel. Questi segnali hanno la funzione di attivare il circuito di alimentazione ausiliaria APWR e il circuito che atttiva la comunicazione radio RPWR, possiamo gestirli via software oppure aggiungere dei pulsanti a questo scopo. In ogni caso i due segnali in output della Nucleo devono essere adattati al livello logico della Driver-Board da 3v3 a 5V, a questo scopo utilizzeremo un HCT541.

- Segnale di **Charge port detect**, cioè il pin 13 non è gestito lato MCU-Board, possiamo decidere di mapparlo o meno in base agli sviluppi futuri. Il segnale proveniente dalla Driver-Board verso la Nucleo deve essere adattato da 5V a 3v3, a questo scopo utilizzeremo un LVC541A.
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

- Segnali di **Analog Input**,  cioè i pin 24 e 26, sono dei segnali provenienti da due sensori di temperatura collegati al connettore J38, i quali forniscono la temperatura. Tuttavia nella configurazione del Pioneer di cui siamo in possesso i sensori di temperatura non sono presenti.
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.
Inoltre sulla Driver-Board è presente un legenda (mostrata in figura), nella quale viene definita la configurazione necessaria per ottenere i dati specifici. Nonostante ciò sulla Driver-Board le resistenze mostrate nella legenda non sono presenti e fungono da circuito aperto verso i pin AN1 e AN2 del connettore J28.
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

- Segnali dei **sensori IR**, cioè i pin 15, 16, 17, 18, 19, 20 provenienti dalla Driver-Board verso la Nucleo devono essere adattati da 5V a 3v3, a questo scopo utilizzeremo un LVC541A, il quale ha esattamente otto ingressi.
---
Vogliamo gestire tutti i segnali forniti dal connettore **J11**:
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

- Segnali di **Motors Button, Reset Button, Aux power switch e Radio power switch**, cioè i pin 3, 4, 5, 6 provenienti dallo User Control Panel verso la Nucleo devono essere adattati da 5V a 3v3, a questo scopo utilizzeremo un LVC541A.

- Segnale di **Buzzer**, cioè il pin 8, è un segnale che avvisa acusticamente che il microcontrollore sta comunicando con lo User Control Panel, è generato tramite PWM dalla Nucleo, quindi deve essere adattato al livello logico dello User Control Panel da 3v3 a 5V, a questo scopo utilizzeremo un HCT541.

- Segnali **Host serial enable**, **Host serial Trasmit** e **Host serial receive**, cioè i pin 14, 15, 16 sono segnali che permettono la comunicazione tra il il microcontrollore e un PC connesso tramite cavo serial allo User Control Panel. Essendo i segnali seriali a 12V corrispondenti al protocollo RS-232, devono essere adattati per essere scambiati con la Nucleo, in entrambe le direzioni (HDSR e HTXD verso lo User Control Panel, HRCV verso la Nucleo. A questo scopo utilizzeremo il MAX3232.

giuseppe-caliaro, 2025-05-11:
Quindi ora che l'idea della Interface-Board è più chiara, provo a fare un BOM:

### Segnali Input Nucleo
- Un **SN74LVC541A** di **Texas Instruments** per adattare gli otto segnali dai **sensori IR**.
- Un **SN74LVC541A** di  **Texas Instruments** per adattare i quattro segnali di **Encoding**, **Reset button, Motors button, Aux1 button, Aux2 button**.
- Un **SN74LVC541A** di  **Texas Instruments** per adattare i segnali di **E-Stop input, Charge port detect e Motor enable** (_?questione aperta, dobbiamo capire meglio il suo funzionamento, come discusso in precedenza, è un input o output?_)

### Segnali Output Nucleo

- Un **SN74HCT541** di **Texas Instruments** per adattare i segnali i segnali di **Left Motor PWM, Right Motor PWM, Left Motor direction, Right Motor direction, Aux1 power enable, Aux2 radio enable, Buzzer.**

### Segnali comunicazione Seriale

- Un **MAX232** di **Texas Instruments** per adattare i segnali di **Host serial enable** e **Host serial transmit** verso la Driver-Board, e **Host serial receive** verso la Nucleo.

### Regolatore di tensione

- Un **LM3940** di **Texas Instruments** per regolare la tensione da 5V a 3v3.

### Condensatori e resistori
Di seguito condivido le raccomandazioni di alimentazione suggerite dal costruttore nei datasheet dei circuiti integrati utilizzati.
Inoltre, come accennato in laboratorio, probabilmente un Bulk Capacitor in parallelo all'alimentazione dell'Interface-Board migliorerebbe situazioni di voltage dips o voltage spikes

- **MAX3232**
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
---
- **LVC541A**
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
---
- **LM3940**
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
---
- **HCT541**
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
---

Inoltre, per ogni integrato, il datasheet suggerisce nella sezione "_Layout Guidelines_" come è preferibile posizionare l'integrato per assicurare le performance massime dello stesso.
Seguirò e documenterò queste procedure quando condividerò lo schema finale.

giuseppe-caliaro, 2025-05-12:
Come accennato precedentemente, la seconda funzione della Interface-Board è quella di permettere un alloggio fisico alla Nucleo.
###  Alloggio Nucleo

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

Come mostrato in figura nel riquadro verde, il Pioneer ha uno slot per la predisposizione della MCU-Board, inoltre la posizione del connettore J28 (collegato in figura) e del connettore J11, determinano la lunghezza precisa dei ribbon cable, perciò al fine di riutilizzare i ribbon già in dotazione, mi sembra sensato mantenere sulla nostra Interface-Board la stessa posizione dei connettori presenti sulla MCU-Board proprietaria.
Di conseguenza mi sembra corretto utilizzare lo slot della MCU-Board proprietaria anche per la nostra Interface-Board, a tale scopo le dimensioni esatte della Interface-Board dovranno essere esattamente quelle della MCU-Board, cioè 20,2 cm x 8,9 cm. Fortunatamente, come visto in laboratorio, la Nucleo rientra perfettamente in queste dimensioni, e per mantenere, come spiegato prima, la stessa posizione dei connettori, la Nucleo deve essere disposta nel seguente modo:

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
Come spiegato prima, in questo modo manteniamo i ribbon che abbiamo a disposizione, e la nostra Interface-Board sarà estraibile comodamente dal suo slot senza doverla smontare e rimontare ogni volta.

Nello schema condiviso, gli integrati saranno posizionati _sotto_ la Nucleo, mentre la gestione dell'alimentazione (cioe LM3940) sarà come suggerito da datasheet vicino all'alimentazione dell'Interface-Board

giuseppe-caliaro, 2025-05-15:
Condivido un primo circuito di come ho progettato l'Interface-Board.
Dato il numero elevato di segnali da gestire, il pannello principale è un diagramma a blocchi, il quale "nasconde" l'implementazione sottostante di ogni blocco mostrandone solo i segnali che ogni blocco ha in ingresso e uscita.

**_Interface-Board: Principale_**
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

Ho diviso il circuito nei seguenti blocchi:
Connettore J11
Connettore J28
Buffer MAX2323
Buffer LCV541A
Buffer HCT541
Connettore CN11 Nucleo

giuseppe-caliaro, 2025-05-15:
Condivido lo schema che ho progettato relativo alla Interface-Board.
Dovendo gestire una quantità elevata di segnali, il foglio root principale dello schema Kicad è un diagramma a blocchi, che nasconde l'implementazione sottostante e mostra solamente i segnali in entrata e uscita dai blocchi:

**_Interface-Board: Principale_**
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

Nello schema sono presenti i seguenti schemi:

- **Connettore J11**:
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

- **Connettore J28:**
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

- **Buffer Serial:**
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

- **Buffer LVC541A:**
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

- **Buffer HCT541:**
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

- **Power Management:**
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

- **Connettore Morpho CN11:**
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

- **Connettore Morpho CN12:**
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

---
Come abbiamo discusso in laboratorio, per diminuire la complessità della Interface-Board gestiremo solo i segnali che permettono un controllo di base del Pioneer (tralasciando quindi sensori IR, conunicazione seriale ecc.), l'Interface-Board sarà composta dall'IC LVC541A che bufferizza i seguenti segnali:
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
L'HCT541 che bufferizza i segnali:
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
Ovviamente i blocchi dei connettori e Power Management sono inclusi.
---
Oltre a questo abbiamo risolto la questione **Motor Enable**, constatando che è messo a GND attraverso una resistenza di Pull-Down, quindi è stato inserito nella progettazione ma poi non è stato implementato.

giuseppe-caliaro, 2025-05-15:
### Considerazioni alloggio Interface-Board
Come detto precedentemente, l'alloggio della Interface-Board sarà lo slot predisposto per la MCU-Board, la quale sarà sostituita.
Al fine di provare a progettare una PCB, abbiamo constatato che è sensato posizionare la Nucleo sul retro della Interface-Board, in modo tale da avere su di un lato gli IC e le piste e i piedini dei Morpho della Nucleo (CN11 e CN12), e sull'altro lato la Nucleo.

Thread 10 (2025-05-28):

PCB Interface-Board

giuseppe-caliaro, 2025-05-28:
Durante la progettazione della PCB ho tenuto conto delle seguenti informazioni:

- Le dimensioni equivalgono a quelle delle MCU-Board proprietaria, cioè 20,2cm x 8,9cm.
- La posizione dei connettori replica quella della MCU-Board proprietaria, al fine di riutilizzare gli stessi ribbon cable senza problemi.
- Al fine di rendere più semplice la progettazione, sono stati gestiti solo i segnali che permettono un controllo di base del Pioneer, cioè segnali di **PWM**, **direzione** e di **encoding** dei motori, e i segnali che gestiscono i **led** e i **pulsanti** sullo user control panel.
- Come ampiamente discusso nelle Issue precedenti, sulla board sono presenti **tre integrati.**
Due **buffer** e un **regolatore di tensione**, **due connettori** che permettono il collegamento con driver-board e user control panel, **un connettori**e al quale arrivano tutti i segnali che non gestiamo, così da poterli utilizzare per implementazioni future.
Infine è presente il connettore a tre pin di alimentazione, e **quattro condensatori**, due per i Vcc dei buffer, uno in parallelo all'alimentazione principale dell'interface-board e uno all ingresso del connettore J11, questo per stabilizzare l'alimentazione dello user control panel.

- La Nucleo sarà posizionata sul retro della board, tramite i connettori CN11 e CN12.

- Per quanto possibile ho cercato di utilizzare la tecnologia THT, come per i condensatori e connettori, purtroppo per quanto riguarda i buffer, li ho trovati solo in SMD, per via della loro dimensione esistono solo SMD.

- Le piste sono state create con un plug-in chiamato FreeRouting, purtoppo per questione di tempo non ho potuto studiare appronditamente abbastanza da farlo manualmente, dovremmo controllarlo lato alimentazione e masse, (per quanto riguarda i segnali penso sia ok, semplicemente quando si incrociano li fa passare nel layer sopra/sotto).
Il plug-in è configurabile, quindi si possono dare in input dei parametri per quanto riguarda le piste e le vie. Potremmo anche tenere le piste e vie generate dal plug-in, controllarle, modificare eventualmente le dimensione delle piste ad esempio di alimentazione e così via.

Condivido gli screenshot dei due layer:

**F.Cu**
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

**B.Cu**
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

giuseppe-caliaro, 2025-05-29:
Studiando meglio i datasheet dei buffer, sembra che dell'HCT541 esiste la versione SN74HCT541N, la quale è costruita con il package PDIP-N, quindi THT.
Per quanto riguarda l'LVC541A, purtroppo non lo trovo in un package che non sia SMD.
Quindi possiamo discutere se vale la pena prenderli in due package diversi oppure prenderli dello stesso package (in questo caso quindi entrambi SMD).

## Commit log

2025-02-10 Simplified sheet tree; fixed all labels
    [buf_conn.kicad_sch, driver_l.kicad_sch, driver_r.kicad_sch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]
2025-02-12 Add IRF5303 symbol and datasheet Add power distribution and generation Fix several issues related to power distribution Rework unused buffers Fix grounding and pull-downs
    [driver_l.kicad_sch, driver_r.kicad_sch, p3dx.kicad_sch]
2025-02-20 Fix main power distribution (+24V->+VBATT) and generation Use standard form for amplifiers Update date
    [driver_l.kicad_sch, driver_r.kicad_sch, p3dx.kicad_sch]
2025-03-26 Add documentation for P3DX driver board
    - system_interconnection.jpg: System-level interconnection diagram showing the wiring and connections between different components of the P3DX driver board.
    - pioneer3_operations_manual.pdf: Comprehensive operations manual for the Pioneer 3 robot, including detailed instructions on setup, usage, and maintenance.
    - appendixB_motor-power_distribution_board.pdf: Appendix B from the Pioneer 3 manual, detailing the motor power distribution board, including schematics and pinout information.
2025-03-28 Update driver motor scheme
    [driver_l.kicad_sch, driver_r.kicad_sch, p3dx.kicad_sch]
2025-03-28 Upgrad left driver scheme
    [driver_l.kicad_sch, driver_r.kicad_sch, p3dx.kicad_sch]
2025-04-01 Update J28 pin name
    [driver_l.kicad_sch, driver_r.kicad_sch, p3dx.kicad_sch]
2025-04-08 Update driver scheme and added User Control Panel scheme
    [74HC00.scheme.kicad_sch, button_sch.kicad_sch, buzzer_sch.kicad_sch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]
